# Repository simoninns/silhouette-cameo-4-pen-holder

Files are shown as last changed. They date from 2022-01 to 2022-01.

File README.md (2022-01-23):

# Silhouette Cameo 4 Pen Holder
## Overview
A 3D printable pen-holder tool for the Silhouette Cameo 4 cutter designed to be as attractive, functional and useful as the original manufacturer's part.

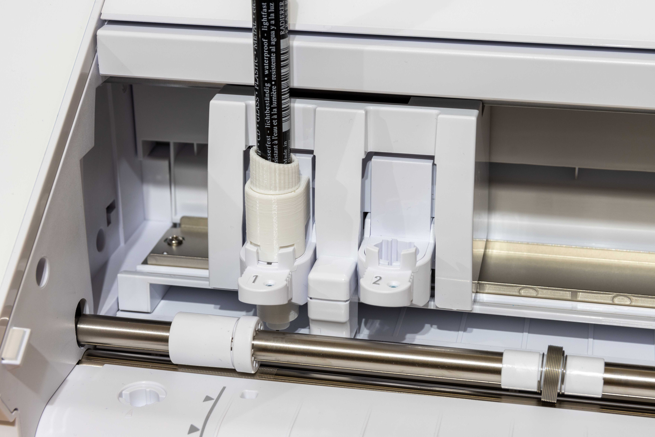
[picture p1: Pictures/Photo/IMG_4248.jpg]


As per the original holder, this version comes with small, medium and large pen-holders and a cap to easily set the correct level for the pen nib.

The whole design is 3D printable with no need for any addition hardware.

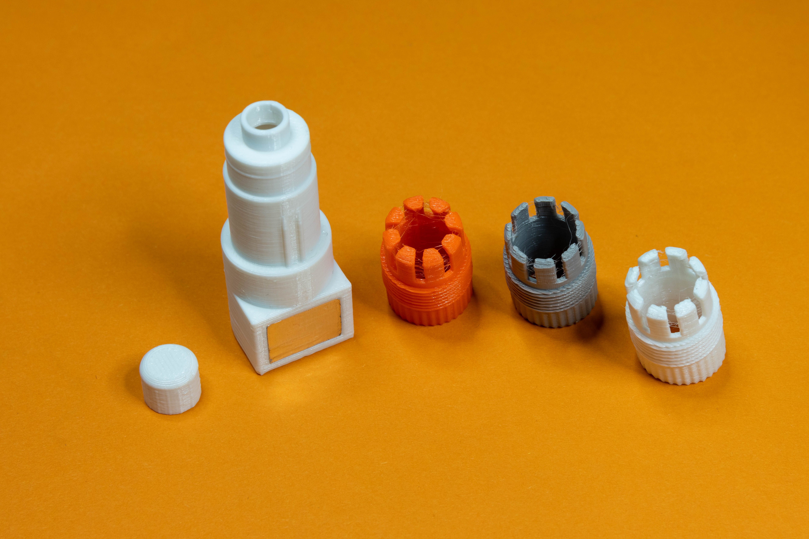
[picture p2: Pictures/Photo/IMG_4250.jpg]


Note: This project is GPLv3 open-source. The github repository for the model (containing the complete OpenSCAD project) can be found at https://github.com/simoninns/silhouette-cameo-4-pen-holder

## Printing instructions
The model has been printed and tested on the Prusa MK3S/MMU2S printer using Prusament PETG filament. All parts fit on a 20x20 printing bed.

Note that the inserts are designed to be printed with the knurled end on the print bed with the rest of the parts at an angle.  This ensures that the layers are diagonal to the pressure on the pen (otherwise the part would simply snap as you inserted it).

The original manufacturer's part uses blue for the small insert, white for the medium and grey for the large.  The overall body (and cap) are both white.

### Recommended print settings

Print settings (for Prusa Slicer) are the same for all included parts:

* Material: PETG
* Layer: 0.20mm (Quality)
* Infill: 15%
* Supports: No Supports

## Assembly
Once printed press the cap onto the top of the holder (if it is a little tight, simply put the cap on and off a few times to losen it up).  The pen adapters simply screw in (the thread should be ready-to-go straight off the printer).

## Tool auto-detection
The Cameo 4 uses an automatic tool detection system which is based on the size of a rectangle of aluminium on the back of the tool.  The pen-holder design has a 14x10mm recess for the aluminium.

A Silhouette Studio file is included in the project that can be used to make the required aluminium.  Use 50mm wide aluminium tape (I used tesa proffessional aluminimum tape (strong) which is 50mm x 25m x 50 microns).  Aluminium tape is used in the heating/air con. industry so it's easy to source.

The included file uses the auto-blade with the following settings:

* Blade Depth: 4
* Force: 14
* Passes: 1
* Speed: 5

Simply cut about 150mm of aluminium tape and affix to a cutting board (make sure it's as smooth as possible). Then, after cutting, place 2 pieces (one on top of the other) in the provided recess on the tool.  The Cameo will then auto-detect the pen holder just like the manufacturer's original part.

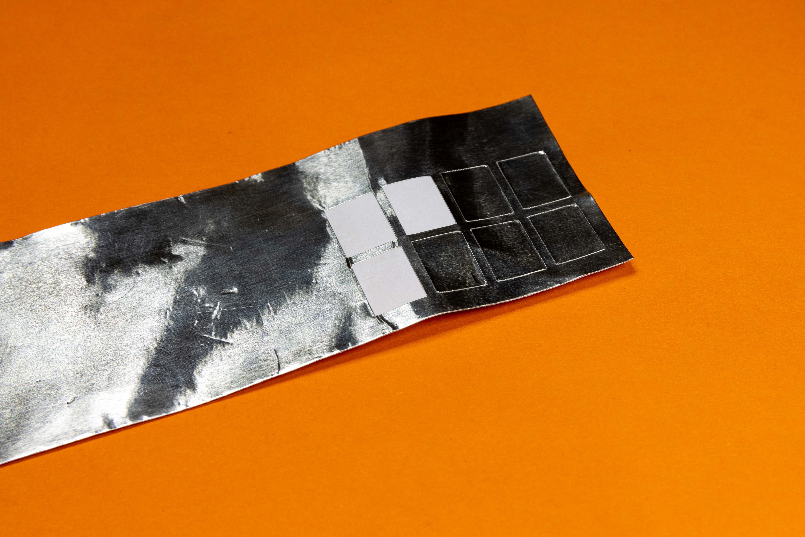
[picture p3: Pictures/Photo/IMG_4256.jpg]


## Author
The Silhouette Cameo 4 Pen Holder is designed and maintained by Simon Inns.

# Licensing
## OpenSCAD source files - software license (GPLv3)

    This is free software: you can redistribute it and/or modify
    it under the terms of the GNU General Public License as published by
    the Free Software Foundation, either version 3 of the License, or
    (at your option) any later version.
    
    This program is distributed in the hope that it will be useful,
    but WITHOUT ANY WARRANTY; without even the implied warranty of
    MERCHANTABILITY or FITNESS FOR A PARTICULAR PURPOSE.  See the
    GNU General Public License for more details.
    
    You should have received a copy of the GNU General Public License
    along with this program.  If not, see <http://www.gnu.org/licenses/>.

## Non-source-code media - Creative Commons license (Creative Commons BY-SA 4.0)
Please see the following link for details: https://creativecommons.org/licenses/by-sa/4.0/

You are free to:

Share - copy and redistribute the material in any medium or format
Adapt - remix, transform, and build upon the material
for any purpose, even commercially.

This license is acceptable for Free Cultural Works.

The licensor cannot revoke these freedoms as long as you follow the license terms.

Under the following terms:

Attribution - You must give appropriate credit, provide a link to the license, and indicate if changes were made. You may do so in any reasonable manner, but not in any way that suggests the licensor endorses you or your use.

ShareAlike - If you remix, transform, or build upon the material, you must distribute your contributions under the same license as the original.

No additional restrictions - You may not apply legal terms or technological measures that legally restrict others from doing anything the license permits.

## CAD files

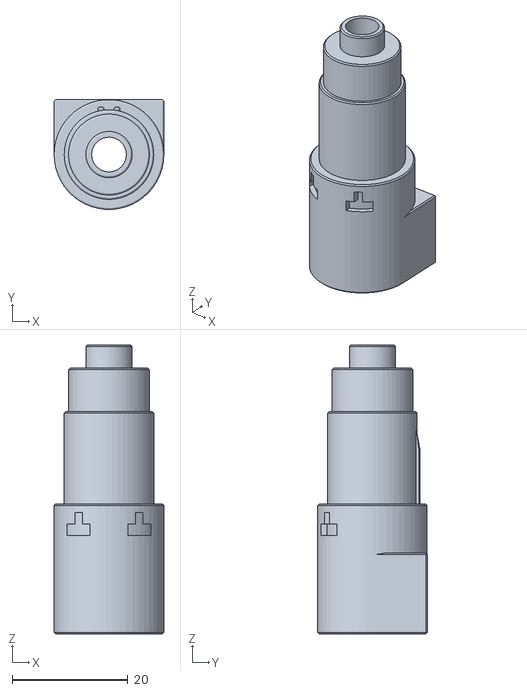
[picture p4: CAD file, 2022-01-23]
stl/pen_holder.stl
19.0 x 19.0 x 50.0

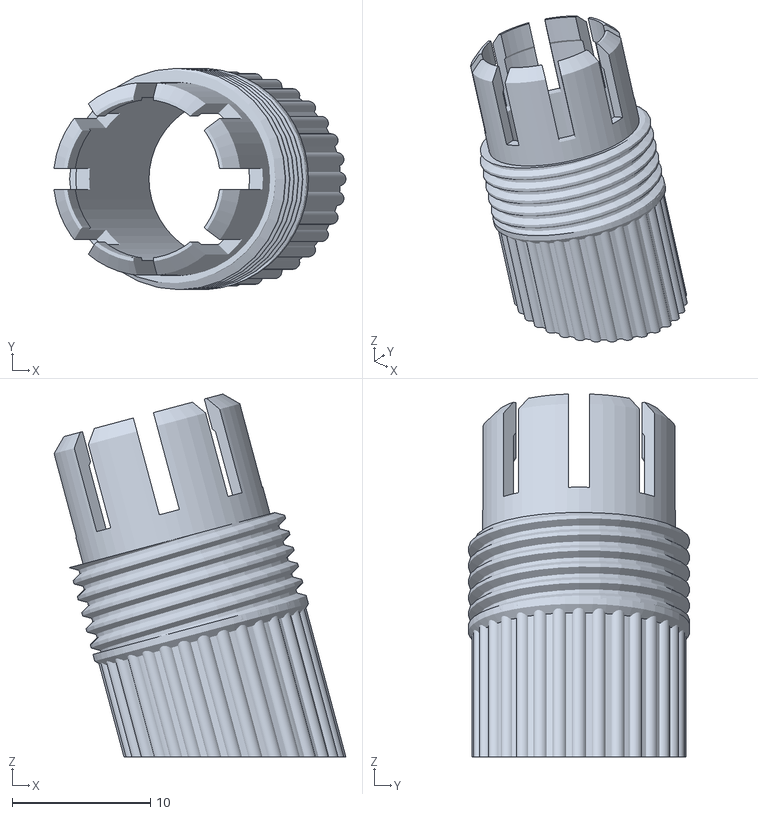
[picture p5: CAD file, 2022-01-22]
stl/insert_large.stl
21.1 x 16.0 x 26.2

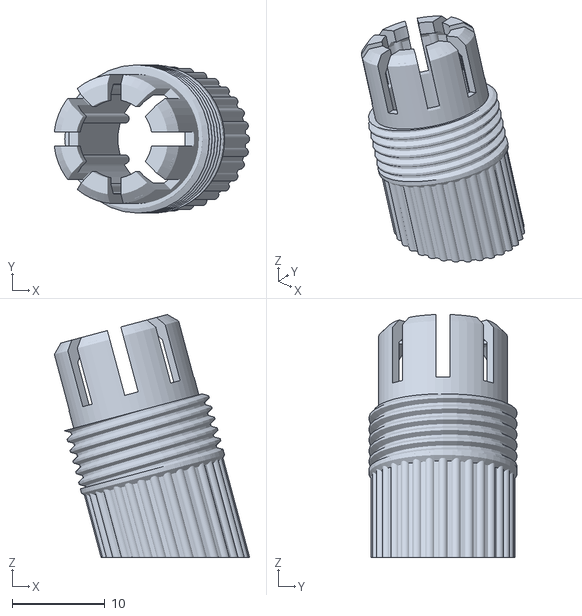
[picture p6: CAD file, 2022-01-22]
stl/insert_small.stl
21.1 x 16.0 x 26.2

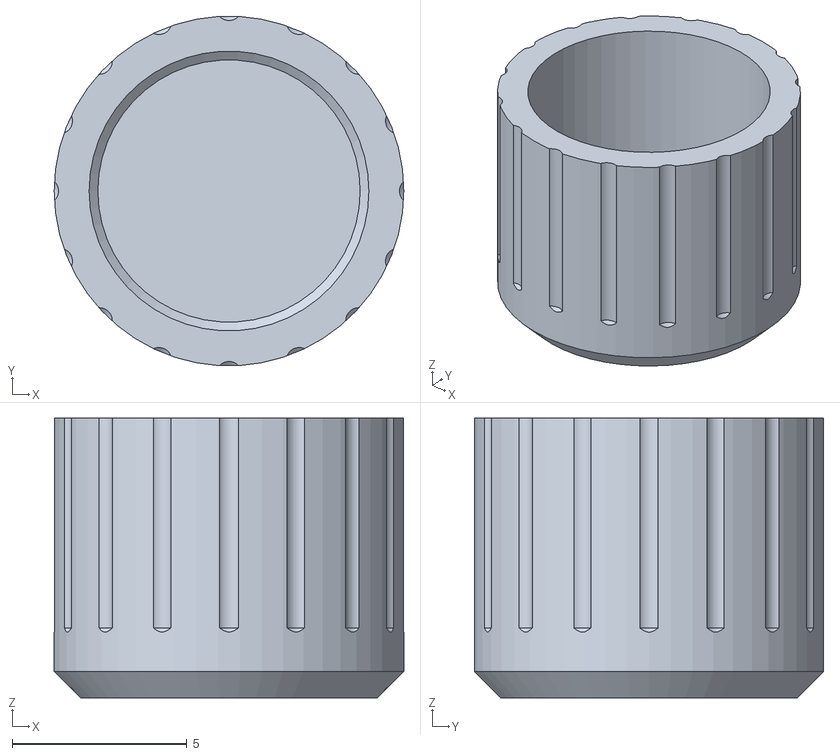
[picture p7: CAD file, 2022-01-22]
stl/cap.stl
10.0 x 9.98 x 8.00

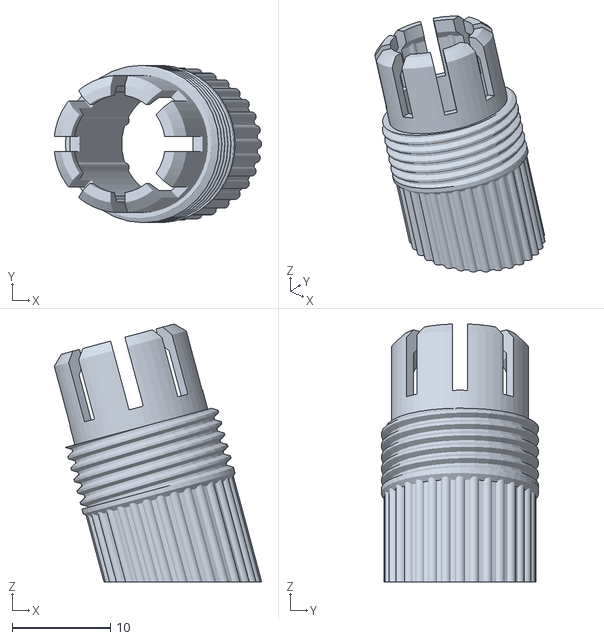
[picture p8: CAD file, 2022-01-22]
stl/insert_medium.stl
21.1 x 16.0 x 26.2

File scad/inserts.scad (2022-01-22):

/************************************************************************

    inserts.scad
    
    Silhouette Cameo 4 Pen Holder
    Copyright (C) 2022 Simon Inns
    
    This is free software: you can redistribute it and/or modify
    it under the terms of the GNU General Public License as published by
    the Free Software Foundation, either version 3 of the License, or
    (at your option) any later version.
    
    This program is distributed in the hope that it will be useful,
    but WITHOUT ANY WARRANTY; without even the implied warranty of
    MERCHANTABILITY or FITNESS FOR A PARTICULAR PURPOSE.  See the
    GNU General Public License for more details.
    
    You should have received a copy of the GNU General Public License
    along with this program.  If not, see <http://www.gnu.org/licenses/>.
	
    Email: simon.inns@gmail.com
    
************************************************************************/

include <BOSL/constants.scad>
use <BOSL/transforms.scad>
use <BOSL/shapes.scad>
use <BOSL/threading.scad>

// Local includes
include <colour_scheme.scad>

module holder_insert_base()
{
    move([0,0,3]) trapezoidal_threaded_rod(d=16, l=7, pitch=1.2, thread_angle=30, internal=false, $fn=32);
    move([0,0,-3.75 - 4]) cyl(h=14, d=14.75, chamfer1=0.25); // Top
    move([0,0,-0.5]) cyl(h=1, d=16, chamfer1=0.5); // Top lip

    // Knurled top outer
    for(rota=[0: 360/32: 360]) { // for(variable = [start : increment : end])
        rotate([0,0,rota]) move([7.25,0,-7]) cyl(h=14, d=1, chamfer=0.25); // Top
    }
}

module holder_insert_small()
{
    difference() {
        union() {
            difference() {
                union() {
                    holder_insert_base();

                    // Top
                    move([0,0,7.75]) cyl(h=16, d=14, chamfer2=1); // Top
                }

                move([0,0,4]) cyl(h=25, d=8.5); // Top minimum diameter
                move([0,0,3.25 - 2]) cyl(h=26, d=12, chamfer2=1); // Main minimum diameter

                // Split up the top so it can contract
                for(rota=[0: 360/8: 360]) {
                    rotate([0,0,rota]) move([0,0,13.5]) cuboid([1.5,20,10]);
                }
            }

            // Knurled top inner
            for(rota=[0: 360/8: 360]) { // for(variable = [start : increment : end])
                rotate([0,0,rota + (360/16)]) move([5.75,0,0]) {
                    cyl(h=30, d=1); // Top
                    move([0.5,0,0]) cuboid([1,1,30]);
                }
            }
        }

    // Cut a 20 degree angle from the base
    move([0,0,-15]) rotate([0,15,0]) cyl(h=10,d=25);
    }
}

module holder_insert_medium()
{
    difference() {
        union() {
            difference() {
                union() {
                    holder_insert_base();

                    // Top
                    move([0,0,7.75]) cyl(h=16, d=14, chamfer2=1); // Top
                }

                move([0,0,4]) cyl(h=25, d=10); // Top minimum diameter
                move([0,0,3.25 - 2]) cyl(h=26, d=12, chamfer2=1); // Main minimum diameter

                // Split up the top so it can contract
                for(rota=[0: 360/8: 360]) {
                    rotate([0,0,rota]) move([0,0,13.5]) cuboid([1.5,20,10]);
                }
            }

            // Knurled top inner
            for(rota=[0: 360/8: 360]) { // for(variable = [start : increment : end])
                rotate([0,0,rota + (360/16)]) move([6.25,0,0]) cyl(h=30, d=1); // Top
            }
        }

    // Cut a 20 degree angle from the base
    move([0,0,-15]) rotate([0,15,0]) cyl(h=10,d=25);
    }
}

module holder_insert_large()
{
    difference() {
        union() {
            difference() {
                union() {
                    holder_insert_base();

                    // Top
                    move([0,0,7.75]) cyl(h=16, d=14, chamfer2=1); // Top
                }

                move([0,0,4]) cyl(h=25, d=11.5); // Top minimum diameter
                move([0,0,3.25 - 2]) cyl(h=26, d=12, chamfer2=1); // Main minimum diameter

                // Split up the top so it can contract
                for(rota=[0: 360/8: 360]) {
                    rotate([0,0,rota]) move([0,0,13.5]) cuboid([1.5,20,10]);
                }
            }
        }

    // Cut a 20 degree angle from the base
    move([0,0,-15]) rotate([0,15,0]) cyl(h=10,d=25);
    }
}

// Blue, small holder
module render_holder_insert_small(crend, toPrint)
{
    if (crend) {
        color(c_blue()) {
            if (toPrint) move([0,0,9]) rotate([0,-15,0]) holder_insert_small();
            else holder_insert_small();
        }
    } else {
        if (toPrint) move([0,0,9]) rotate([0,-15,0]) holder_insert_small();
            else holder_insert_small();
    }
}    

// White, medium holder
module render_holder_insert_medium(crend, toPrint)
{
    if (crend) {
        color(c_white()) {
            if (toPrint) move([0,0,9]) rotate([0,-15,0]) holder_insert_medium();
            else holder_insert_medium();
        }
    } else {
        if (toPrint) move([0,0,9]) rotate([0,-15,0]) holder_insert_medium();
        else holder_insert_medium();
    }
}

// Grey, large holder
module render_holder_insert_large(crend, toPrint)
{
    if (crend) {
        color(c_grey()) {
            if (toPrint) move([0,0,9]) rotate([0,-15,0]) holder_insert_large();
            else holder_insert_large();
        }
    } else {
        if (toPrint) move([0,0,9]) rotate([0,-15,0]) holder_insert_large();
        else holder_insert_large();
    }
}    

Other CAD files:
scad/cap.scad
scad/colour_scheme.scad
scad/main.scad
scad/pen_holder.scad

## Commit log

2022-01-22 Initial commit of project to Github
    [cap.scad, cap.stl, colour_scheme.scad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]
2022-01-22 Added cut file to make tool-detection aluminium and updated readme
2022-01-22 Modified insertion guides on pen holder and changed depth of tool detection recess
    [pen_holder.scad, pen_holder.stl]
2022-01-23 Modified tool detection position slighly read for test
    [pen_holder.scad, pen_holder.stl]
